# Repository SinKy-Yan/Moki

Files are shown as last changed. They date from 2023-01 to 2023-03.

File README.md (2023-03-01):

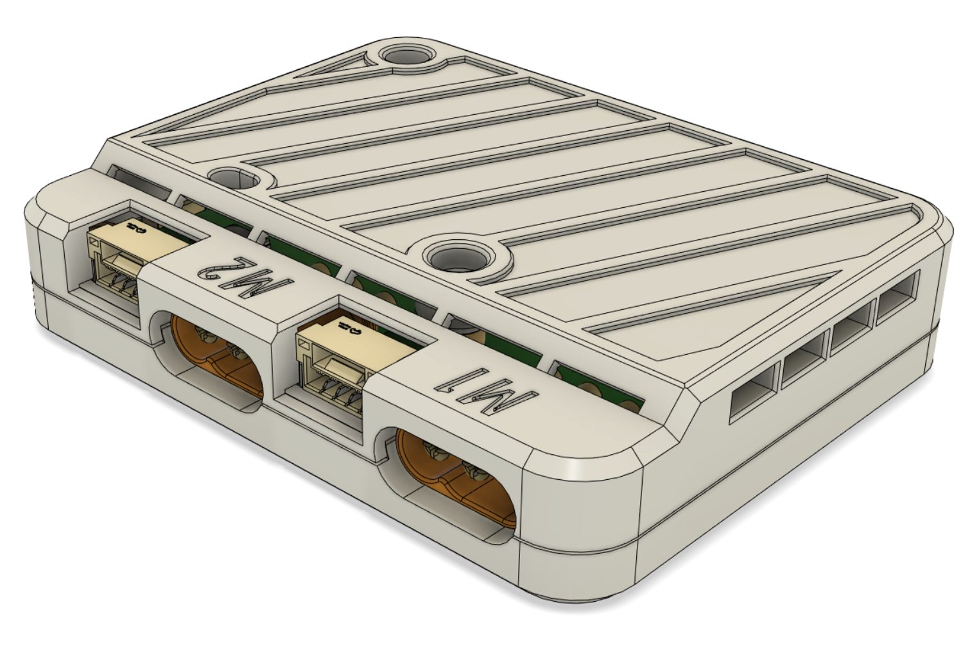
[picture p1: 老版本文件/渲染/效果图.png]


# Moki V3🦄

用于低KV小电流无刷电机的FOC驱动板，配套有设计好的主板外壳和电机外壳，以及连接电机的板子

旨在让电机闭环控制变得更加简单

基于`SimpleFOC`设计

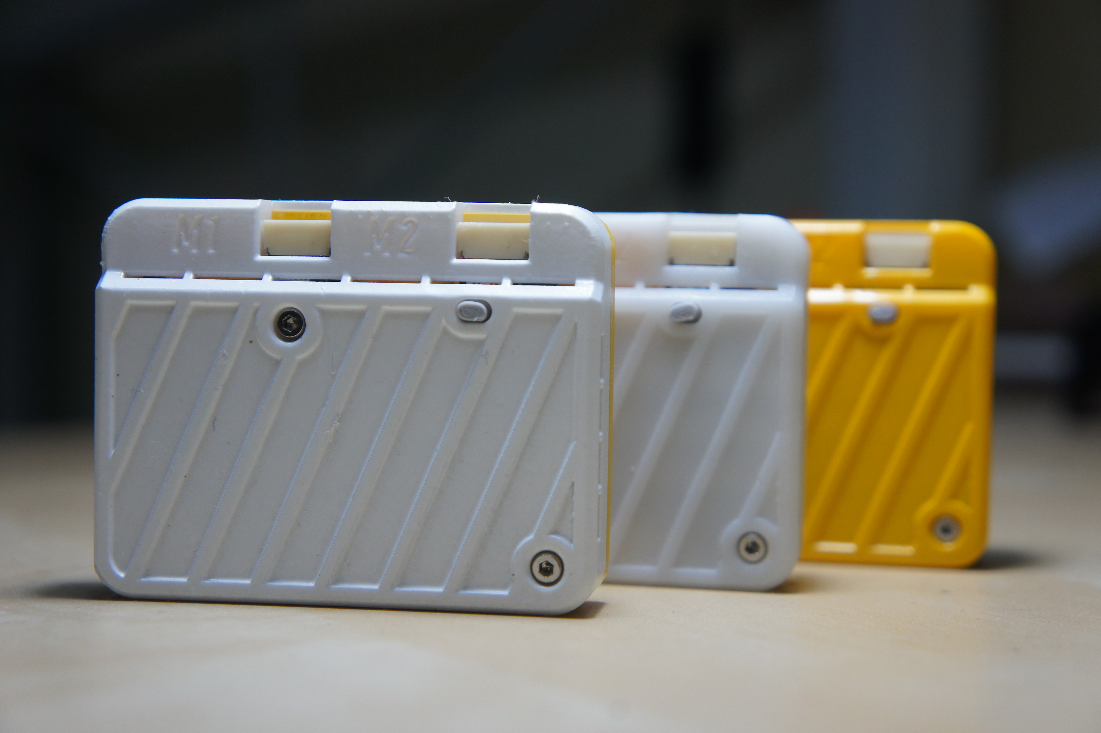
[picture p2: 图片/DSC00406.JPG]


# ⚠️注意

1. 主要设计给`2308`、`4010`云台电机，它们的电流会比那种高转速的电机小很多，大概只有`500ma`，所以我这个板子的走线也没那么粗，也没有加`MOS`管
2. 板子**输入电压范围**为`9v~12v`，设计额定电流单相`1A`
3. 板子上的电流采样电阻的阻值应该根据电机的相电阻而变化，然后在`SimpleFOC`库里配置好，我用的4010电机相电阻12.7Ω用0.5Ω电阻比较合适，但是给2308电机用的话直接转不起来
4. 你需要`m2*4`和`m2*5`的螺丝用于固定外壳
5. 上下两个壳子在三维猴即可打印，并且光固化和FDM都可以打印出来，如果你自己有打印机也可以

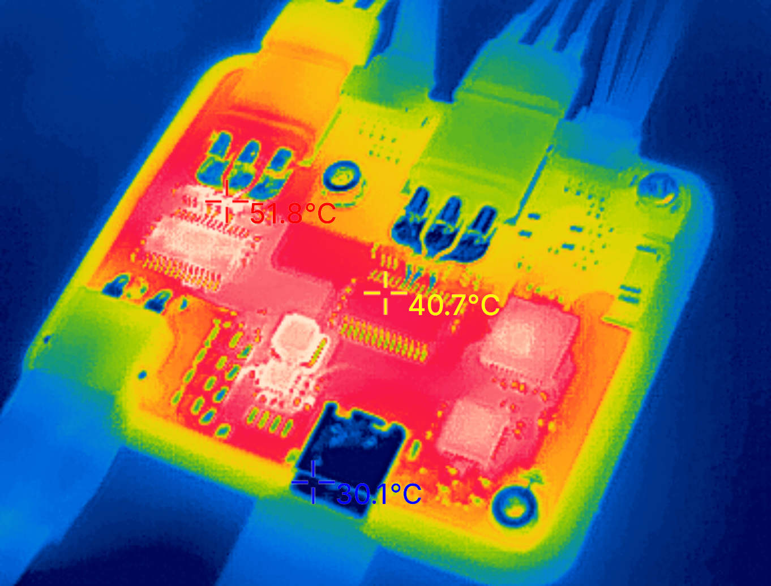
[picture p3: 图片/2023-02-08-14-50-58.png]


# 🙌引脚图

| | 电机1 | 电机2 |
| :---: | :---: | :---: |
| A相PWM |  17 |  14 |
| B相PWM |  18 |  26 |
| C相PWM | 5 |  27 |
| A相电流检测 |  39 | — |
| B相电流检测 |  36 |  35 |
| C相电流检测 | — |  34 |
|  I2C  SDA | 4 |  32 |
|  I2C  SCL |  16 |  33 |

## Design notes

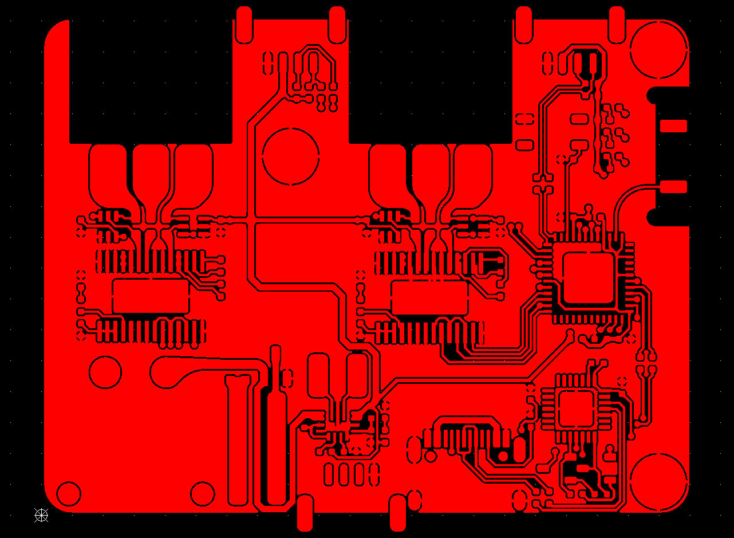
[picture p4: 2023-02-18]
老版本文件/渲染/铺铜.png

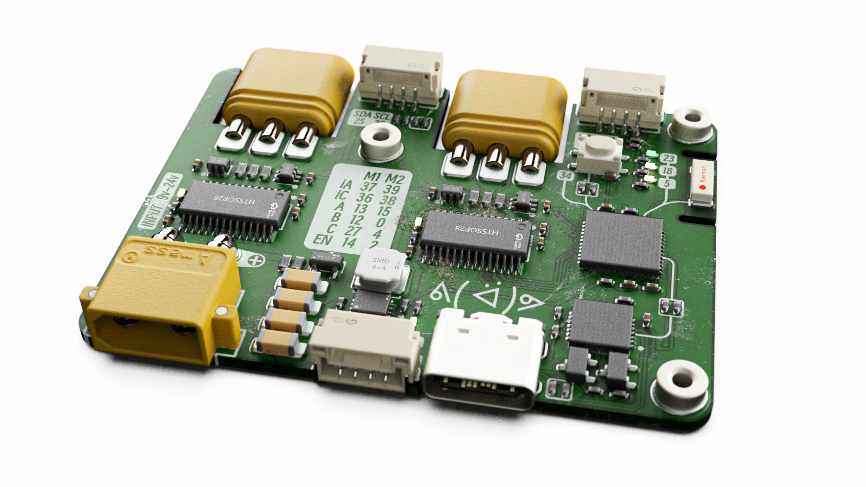
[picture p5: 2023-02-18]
老版本文件/渲染/渲染2.12-3.jpg

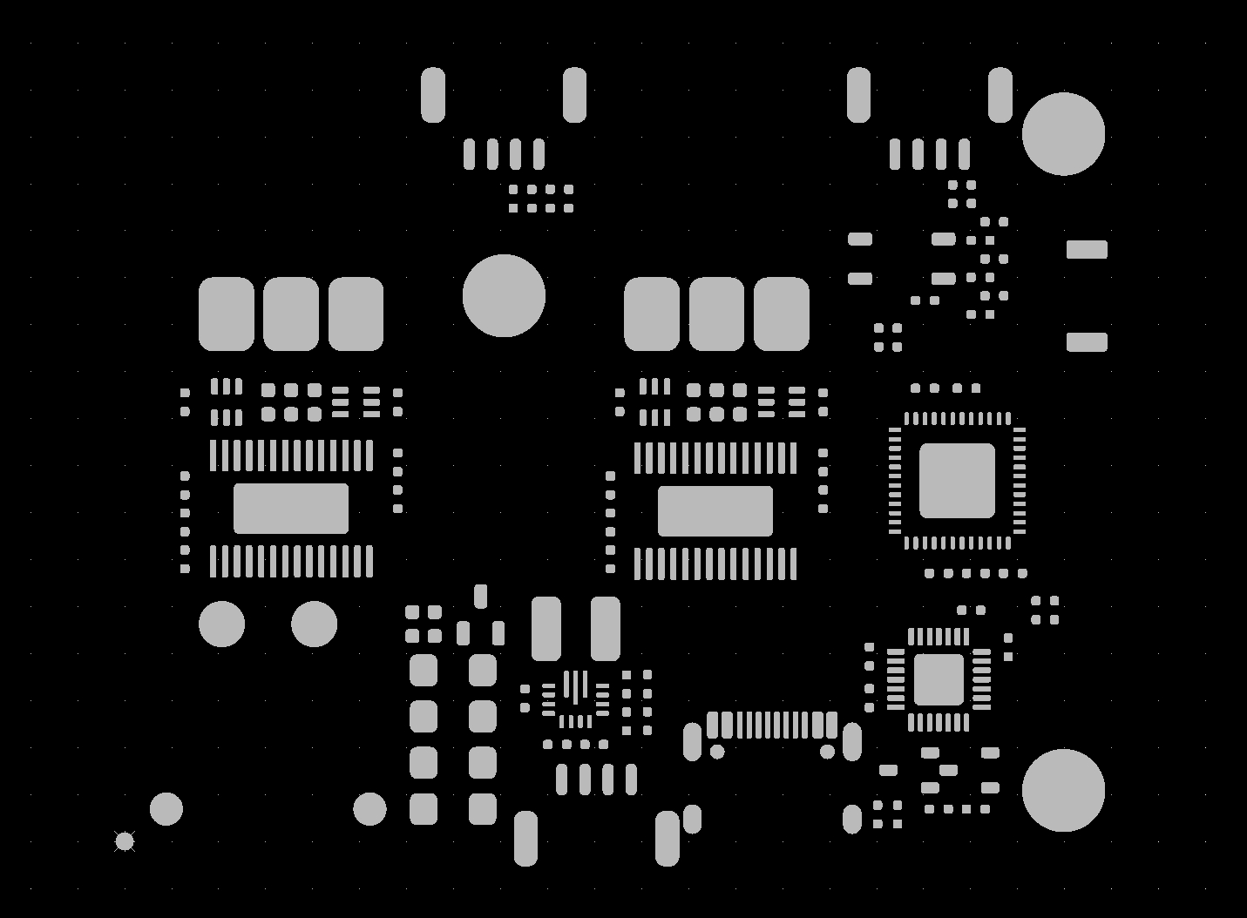
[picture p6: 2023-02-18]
老版本文件/渲染/开窗.jpg

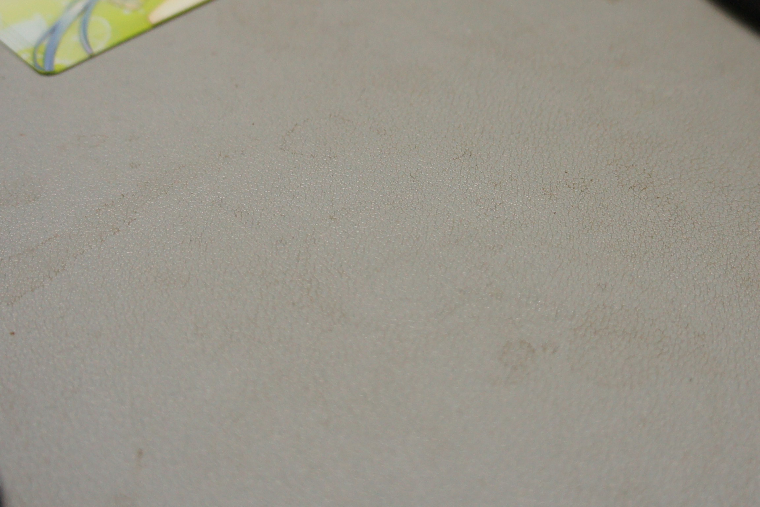
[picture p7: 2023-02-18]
老版本文件/渲染/DSC0rtesfgse0241.JPG

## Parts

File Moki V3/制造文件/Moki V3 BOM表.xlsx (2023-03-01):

说明 | Comment | Description | 位号 | 封装 | 数量
不用wifi可以不加 | AN2051-245 |  | *1 | AN2051-245 | 1
 | S8050 |  | *2, *3 | SOT22-3 | 2
 | CP2102 |  | *4 | QFN-28 | 1
 | 3*4*2.5贴片按键 |  | *6 | SW-SMD_4P-L4.2-W3.3-P2.15-LS5.1 | 1
 | 10uF | 贴片电容/MLCC电容 | C1, C6, C23, C25 | 电容-0402 | 4
 | 0.1uF | 贴片电容/MLCC电容 | C2, C5, C8, C14, C17, C19 | 电容-0402 | 6
 | 0.01uF | 贴片电容/MLCC电容 | C3, C15 | 电容-0402 | 2
 | 1uF | 贴片电容/MLCC电容 | C4, C7, C16, C18 | 电容-0402 | 4
 | 10uF | 贴片电容/MLCC电容 | C9, C10, C11, C12 | C1206 | 4
 | MR30PW-F |  | CN1, CN2 | CONN-TH_MR30-M | 2
 | XT30PW-M | Socket,DCsupply,XT30,male,PIN:2 | CN3 | CONN-TH_XT30PW-M | 1
 | A1257WR-S-4P | 参考系列:GH;间距:1.25mm;插针结构:1x4P;排数:1;每排PIN数:4;行距:-;安装方式:-;触头材质:黄铜; | CN4, CN5, CN6 | CONN-SMD_A1257WR-S-4P | 3
选自己喜欢的颜色 | LED-0402 |  | L1, L2, L3, L4, L5, L6 | LED-0402 | 6
 | SWPA4020S1R5NT | 电感值:1.5uH;精度:±30%;额定电流:1.98A;饱和电流(Isat):4.45A;直流电阻(DCR):35mΩ; | L7 | IND-SMD_L4.0-W4.0 | 1
如果不用固定的话可以不用 | 贴片螺母-m2 |  | nut2, nut3, nut4 | 贴片螺母-m2 | 3
 | AO3400 | 类型:N沟道;漏源电压(Vdss):30V;连续漏极电流(Id):5.8A;功率(Pd):350mW;导通电阻(RDS(on)@Vgs,Id):35mΩ@10V,5.8A;阈值电压(Vgs(th)@Id):1.4V@250uA; | Q1 | SOT-23-3_L2.9-W1.3-P1.90-LS2.4-BR | 1
 | 5.1K | 贴片电阻 | R1, R2, R3, R9, R12, R16, R17, R19, R21 | 电阻-0402 | 9
 | 0 | 贴片电阻 | R4 | 电阻-0402 | 1
 | 10K | 贴片电阻 | R5, R6, R7, R8, R11, R14, R15, R22 | 电阻-0402 | 8
阻值根据自己电机的相电阻选 | 0.5 | 贴片电阻 | R10, R13, R18, R20, R27, R28 | R0603_L | 6
 | 470K | 贴片电阻 | R23 | 电阻-0402 | 1
 | 150K | 贴片电阻 | R24 | 电阻-0402 | 1
 | 100K | 贴片电阻 | R25 | 电阻-0402 | 1
 | 0 | 贴片电阻 | R26, R29 | R0603_L | 2
 | 22 | 贴片电阻 | R30, R31, R32, R33, R34, R35, R36, R37 | 电阻-0402 | 8
 | ESP32-Pico-D4 |  | U1 | QFN-48_7X7 | 1
 | INA199B1DCKR | INA199 26V、双向、零漂移、低侧/高侧、电压输出分流监控器 | U2, U3, U5, U6 | SC-70-6_L2.2-W1.3-P0.65-LS2.1-BL | 4
 | DRV8313PWPR | DRV8313 三路 1/2 H 桥驱动器 IC | U4, U? | HTSSOP-28_L9.8-W4.5-P0.65-LS6.6-BL-EP | 2
 | 5.0SMDJ24CA | 极性:双向;反向截止电压(Vrwm):24V;击穿电压:26.7V;反向漏电流(Ir):5uA;峰值脉冲电流(Ipp)@10/1000μs:129A;最大钳位电压:38.9V;峰值脉冲功率(Ppp)@10/1000μs:5kW; | U8 | SMC_L6.9-W5.9-LS7.9-BI | 1
 | TPS63070RNMR | 功能类型:升降压型;同步整流:是;输出通道数:1;拓扑结构:降压-升压式;输入电压:2V~16V;输出电压:2.5V~9V;输出电流(最大值):2A;开关频率:2.4MHz; | U9 | VQFN-HR-15_L3.0-W2.5-P0.50-BL_TPS63070RNMR | 1
 | TYPE-C 2.0 -16P | USB2.0_Type-C_16Pin母座 | USBC1 | USB-C-SMD_16P | 1

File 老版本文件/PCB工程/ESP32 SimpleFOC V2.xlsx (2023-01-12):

Quantity | Comment | Designator | Footprint
2 | S8050 | *1, *2 | SOT22-3
1 | CP2102 | *3 | QFN-28
2 | 0.01uF | C1, C9 | 电容-0402
6 | 10uF | C2, C5, C7, C12, C14, C15 | 电容-0402
7 | 0.1uF | C3, C4, C6, C8, C10, C11, C13 | 电容-0402
3 | 10uF | C16, C17, C18 | C0603_L
2 | MR30PW-F | CN1, CN2 | CONN-TH_MR30PW-F
1 | XT30PW-M | CN3 | CONN-TH_XT30PW-M
2 | LED-0402 | L1, L2 | LED-0402
3 | GROVE | Q1, Q2, Q3 | GROVE
1 | AO3400_C181090 | Q4 | SOT-23-3_L2.9-W1.3-P1.90-LS2.4-BR
7 | 10K | R1, R2, R3, R4, R7, R9, R10 | 电阻-0402
4 | 0.5 | R5, R8, R13, R14 | R1206
4 | 5.1K | R6, R11, R12, R15 | 电阻-0402
2 | NC | R16, R17 | 电阻-0402
4 | INA199B1DCKR | U1, U3, U5, U6 | SC-70-6_L2.2-W1.3-P0.65-LS2.1-BL
1 | ESP32-WROOM-32 | U2 | ESP32-WROOM-32
2 | DRV8313PWPR | U4, U7 | HTSSOP-28_L9.8-W4.5-P0.65-LS6.6-BL-EP
1 | AMS1117 | U8 | SOT-223-3_L6.5-W3.4-P2.30-LS7.0-BR
1 | TYPE-C 2.0 -16P | USBC1 | USB-C-SMD_16P

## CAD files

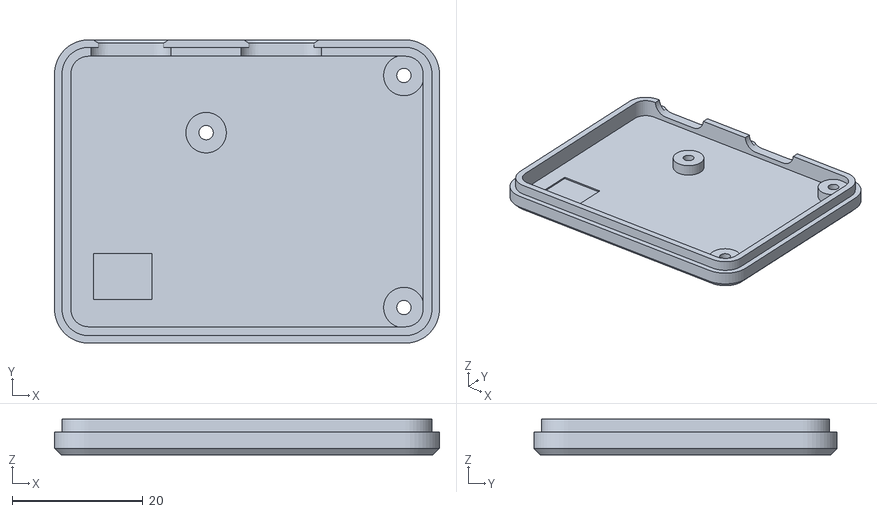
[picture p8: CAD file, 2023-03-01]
Moki V3/制造文件/打印用stl文件/下壳.stl
58.9 x 46.4 x 5.50

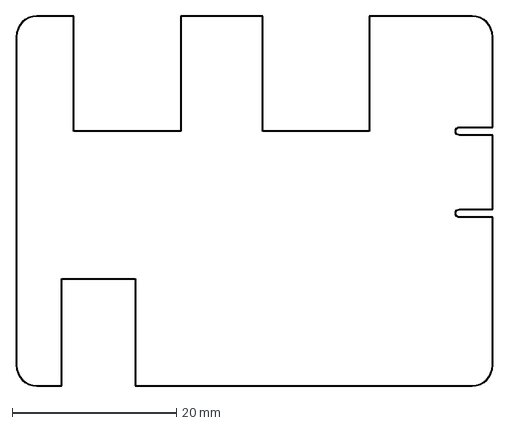
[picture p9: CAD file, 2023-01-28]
Moki V3/源文件/PCB板机械外形.dxf
58.0 x 45.0 mm

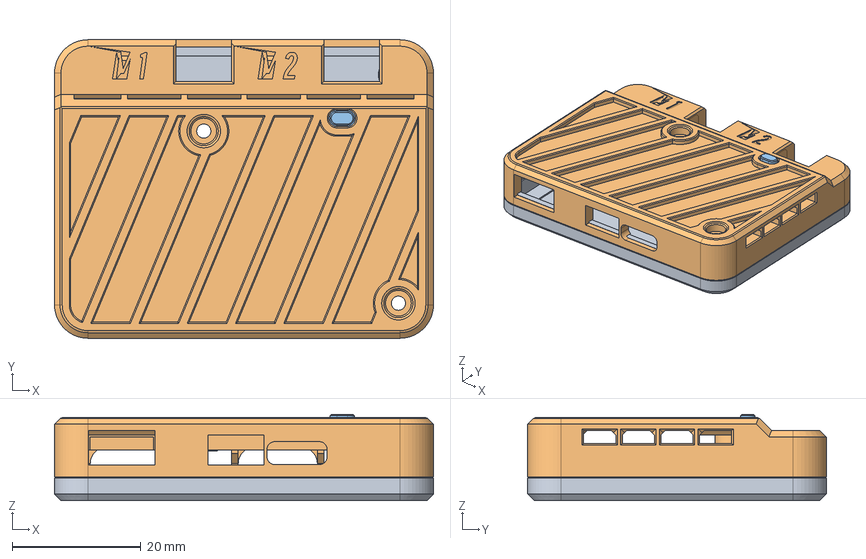
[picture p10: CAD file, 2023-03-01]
Moki V3/源文件/模型/Moki V3 不含PCB.step
58.9 x 46.4 x 13.4 mm
下壳
零部件3
零部件4

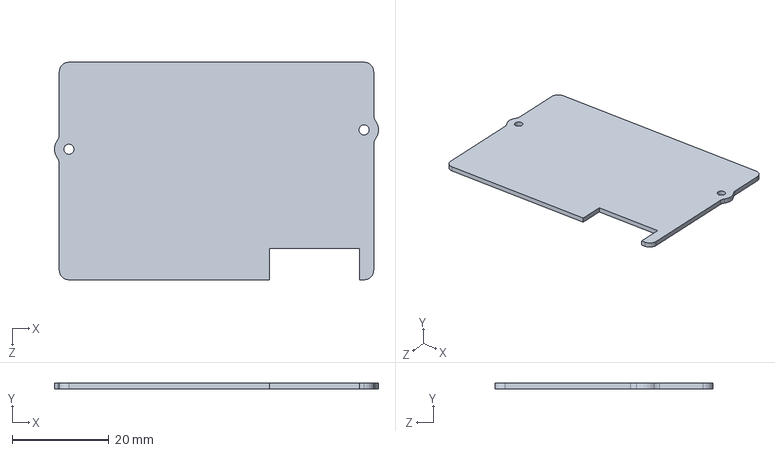
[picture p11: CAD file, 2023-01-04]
老版本文件/PCB工程/PCB机械外形.SLDPRT
67.0 x 1.20 x 45.0 mm

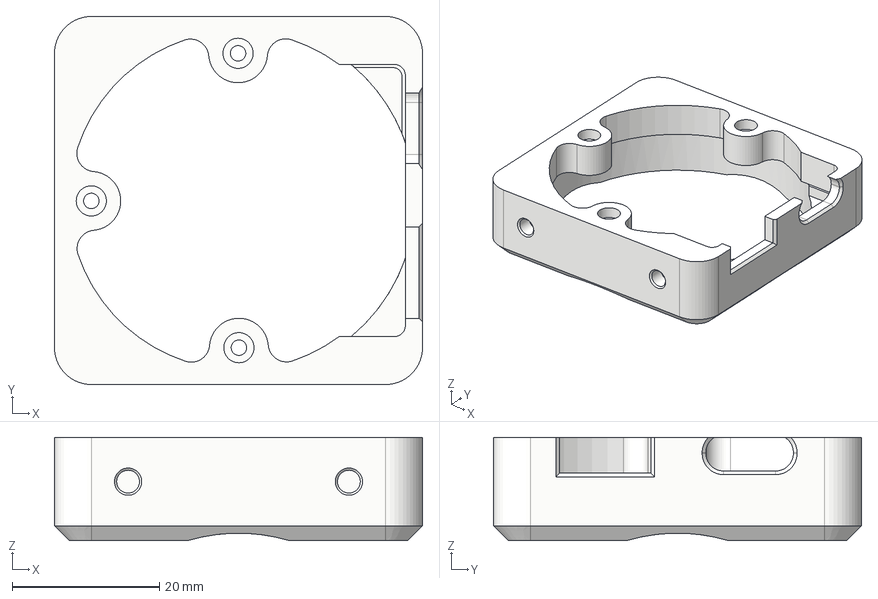
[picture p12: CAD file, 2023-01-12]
老版本文件/外壳模型/电机底座上.step
50.0 x 50.0 x 14.0 mm

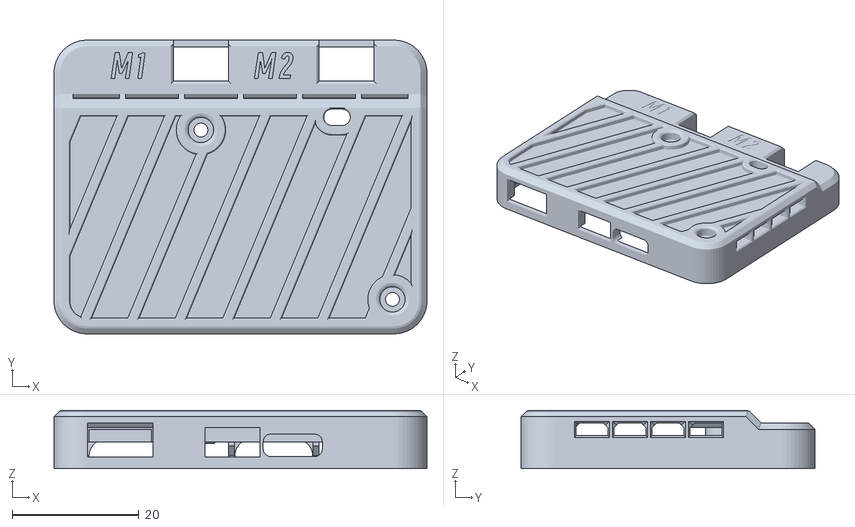
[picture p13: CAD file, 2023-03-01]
Moki V3/制造文件/打印用stl文件/上壳.stl
58.9 x 46.4 x 9.20

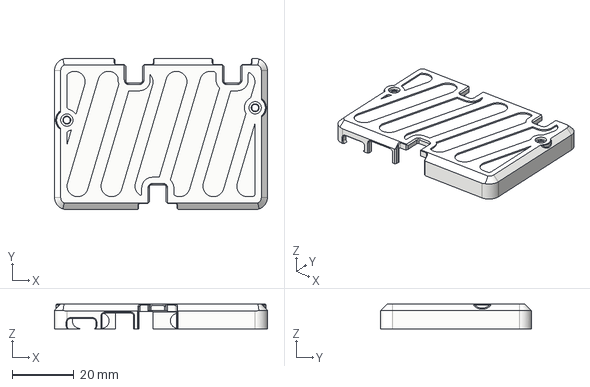
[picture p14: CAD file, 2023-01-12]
老版本文件/外壳模型/驱动板外壳上.step
69.0 x 49.0 x 8.00 mm

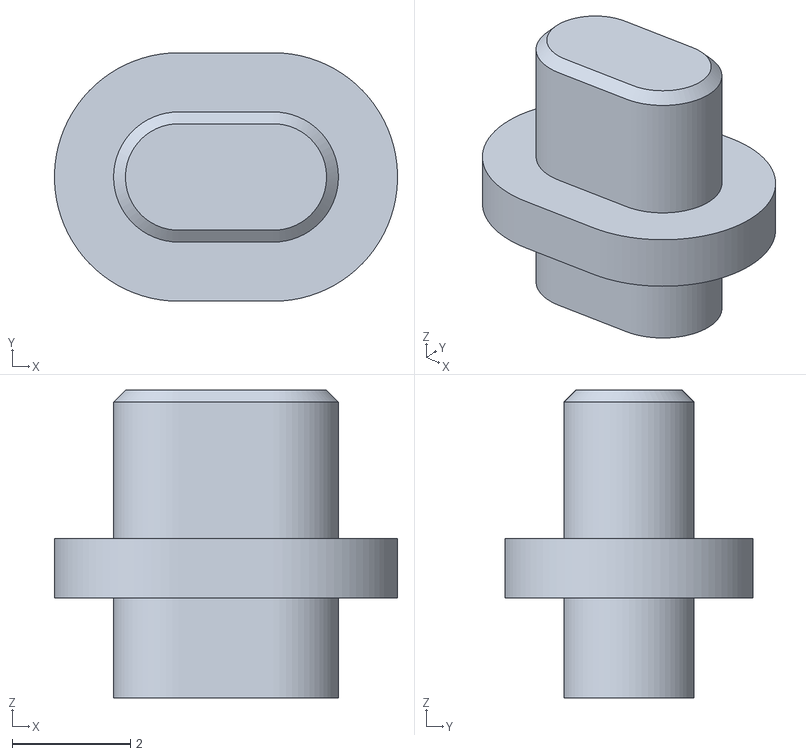
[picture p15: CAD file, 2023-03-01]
Moki V3/制造文件/打印用stl文件/按键.stl
5.80 x 4.20 x 5.20

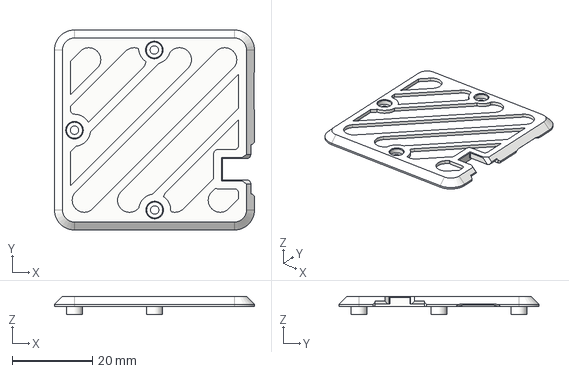
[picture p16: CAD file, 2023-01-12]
老版本文件/外壳模型/电机底座下.step
50.0 x 50.0 x 4.50 mm

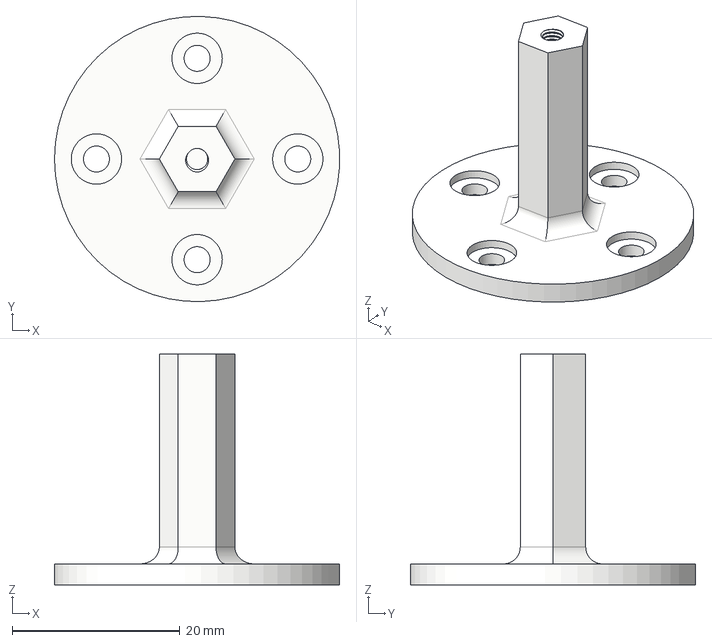
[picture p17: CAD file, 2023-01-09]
老版本文件/外壳模型/电机连轴.step
34.0 x 34.0 x 27.5 mm

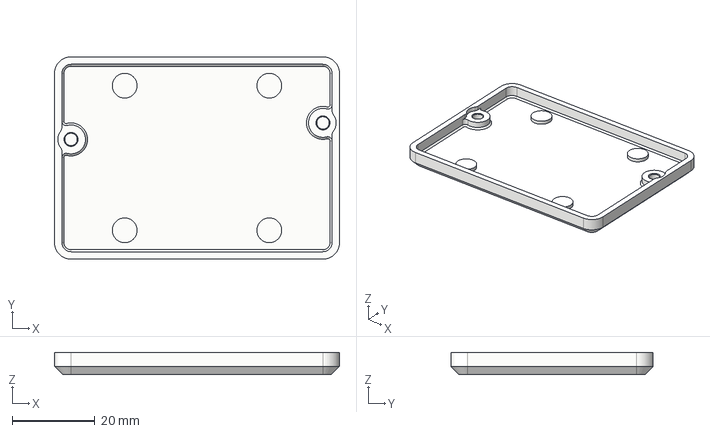
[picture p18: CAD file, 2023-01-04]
老版本文件/外壳模型/驱动板外壳下.step
69.0 x 49.0 x 5.43 mm

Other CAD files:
老版本文件/PCB工程/PCB机械外形.DXF

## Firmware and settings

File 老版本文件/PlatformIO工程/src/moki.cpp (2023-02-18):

#include "Moki.h"
#include "Arduino.h"
#include <SimpleFOC.h>

#ifndef m1_offset
#warning 未设置电机1的机械偏差,将会在开机的时候自动检测
#define m1_offset -1
#endif

#ifndef m2_offset
#warning 未设置电机2的机械偏差,将会在开机的时候自动检测
#define m2_offset -1
#endif

/* 定义IO口,不要动 */
MagneticSensorI2C sensor1 = MagneticSensorI2C(AS5600_I2C);
MagneticSensorI2C sensor2 = MagneticSensorI2C(AS5600_I2C);
BLDCMotor motor1 = BLDCMotor(11, 12.5, 74);
BLDCDriver3PWM driver1 = BLDCDriver3PWM(13, 12, 27, 14);
BLDCMotor motor2 = BLDCMotor(11, 12.5, 74);
BLDCDriver3PWM driver2 = BLDCDriver3PWM(15, 0, 4, 2);

/* 串口控制 */
Commander command = Commander(Serial);
void onMotor1(char *cmd) { command.motor(&motor1, cmd); }
void onMotor2(char *cmd) { command.motor(&motor2, cmd); }

Moki::Moki(int number_of_motor)
{
    this->number_of_motor = number_of_motor;
}

/* 初始化Moki(无传入变量) */
void Moki::setup()
{
    /* ESP32通信接口设置 */
    setCpuFrequencyMhz(Cpu_Frequency);
    Serial.begin(115200);
    Serial1.begin(115200, SERIAL_8N1, 21, 22);

    /* 板载LED设置 */
    // xTaskCreatePinnedToCore(Task1code, "Task1", 10000, NULL, 1, NULL, 1);
    // ledcSetup(1, 1000, 8);  // 设置LEDC通道8频率为1,分辨率为10位,即占空比可选0~1023
    // ledcAttachPin(2, 1); // 设置LEDC通道8在IO14上输出
    // ledcWrite(1, 1000);

    command.add('A', onMotor1, "设定电机1");
    command.add('B', onMotor2, "设定电机2");

    if (this->number_of_motor == 1)
    {
        init_m1();
    }
    else if (this->number_of_motor == 2)
    {
        init_m1();
        init_m2();
    }
}

/* 启动FOC控制(无传入变量) */
void Moki::run(int number_of_example)
{
    if (this->number_of_motor == 1)
    {
        run_m1();
    }
    else if (this->number_of_motor == 2)
    {
        run_m1();
        run_m2();
    }
    command.run();
}

void Moki::run_m1()
{
    // if (sensor1.getAngle() > 0.00 or sensor1.getAngle() < 2.00)
    // {
    //     motor1.voltage_limit = 0;
    //     Serial.println(sensor1.getAngle() - 0);
    // }
    // else if (sensor1.getAngle() < 0.00)
    // {
    //     motor1.voltage_limit = 2;
    //     motor1.move(0);
    // }
    // else if (sensor1.getAngle() > 2.00)
    // {
    //     motor1.voltage_limit = 2;
    //     motor1.move(2);
    // }

    motor1.loopFOC();
    motor1.move();
    // Serial.println(sensor1.getAngle());
}

void Moki::run_m2()
{
    motor2.loopFOC();
    motor2.move();
}

void Moki::init_m1()
{
    Wire.begin(25, 26, (uint32_t)i2c_Frequency);
    sensor1.init();
    motor1.linkSensor(&sensor1);
    driver1.voltage_power_supply = power_supply_voltage;
    driver1.init();
    motor1.linkDriver(&driver1);
    motor1.foc_modulation = FOCModulationType::SinePWM;
    motor1.torque_controller = TorqueControlType::voltage;
    motor1.controller = MotionControlType::Motion_Control_Type;
    // Serial.println("已设置m1的驱动器和传感器");

    motor1.PID_velocity.P = 0.1;
    motor1.PID_velocity.I = 0.2;
    motor1.PID_velocity.D = 0;
    motor1.PID_velocity.output_ramp = 50;
    motor1.LPF_velocity.Tf = 0.1;
    motor1.velocity_limit = 20;
    motor1.voltage_limit = motor_voltage_limit;
    motor1.current_limit = 0.3;
    motor1.P_angle.P = 20;
    motor1.P_angle.I = 0;
    motor1.P_angle.D = 0;
    motor1.P_angle.output_ramp = 500;
    motor1.LPF_angle.Tf = 0;
    // Serial.println("已设置m1的控制参数");

    motor1.init();

    if (m1_offset == -1)
    {
        Serial.println("未设置m1机械偏差,开始自检");
        motor1.initFOC();
    }

    else
    {
        Serial.println("已设置m1机械偏差,跳过自检");
        motor1.initFOC(m1_offset, Direction::CCW);
    }
    Serial.println("m1初始化完成");

    motor1.target = Target;
}

void Moki::init_m2()
{
    Wire1.begin(33, 32, (uint32_t)i2c_Frequency);
    sensor2.init(&Wire1);
    motor2.linkSensor(&sensor2);
    driver2.voltage_power_supply = power_supply_voltage;
    driver2.init();
    motor2.linkDriver(&driver2);
    motor2.foc_modulation = FOCModulationType::SinePWM;
    motor2.torque_controller = TorqueControlType::voltage;
    motor2.controller = MotionControlType::Motion_Control_Type;
    // Serial.println("已设置m2的驱动器和传感器");

    motor2.PID_velocity.P = 0.1;
    motor2.PID_velocity.I = 0.2;
    motor2.PID_velocity.D = 0;
    motor2.PID_velocity.output_ramp = 50;
    motor2.LPF_velocity.Tf = 0.1;
    motor2.velocity_limit = 20;
    motor2.voltage_limit = 6;
    motor2.current_limit = 0.3;
    motor2.P_angle.P = 20;
    motor2.P_angle.I = 0;
    motor2.P_angle.D = 0;
    motor2.P_angle.output_ramp = 500;
    motor2.LPF_angle.Tf = 0;
    // Serial.println("已设置m2的控制参数");

    motor2.init();

    if (m1_offset == -1)
    {
        Serial.println("未设置m2机械偏差,开始自检");
        motor2.initFOC();
    }

    else
    {
        Serial.println("已设置m2机械偏差,跳过自检");
        motor2.initFOC(m2_offset, Direction::CCW);
    }

    Serial.println("m2初始化完成");

    motor2.target = Target;
}

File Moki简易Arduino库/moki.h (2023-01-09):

#include <Arduino.h>
#ifndef Moki_h
#define Moki_h
#define VERSION = 0.1

/* 自定义用的参数 */
// #define m1_offset 4.71               /* 电机1的机械偏差,不知道的话设为-1 */
// #define m2_offset 5.47               /* 电机2的机械偏差,不知道的话设为-1 */
#define power_supply_voltage 10      /* 供电电压 */
#define Cpu_Frequency 80             /* ESP32的CPU频率 */
#define i2c_Frequency 400000         /* i2c的速率 */
#define Motion_Control_Type velocity /* 默认控制模式(torque、velocity、angle) */
#define Target 5                     /* 初始化之后的电机目标 */
#define motor_voltage_limit 6        /* 电机电压限制 */

/* Moki驱动库 */
class Moki 
{
    private:
        void run_m1();
        void run_m2();
        void init_m1();
        void init_m2();
        int number_of_motor;

    public:
        void setup();
        void run(int number_of_example);
        Moki(int number_of_motor);
};
#endif
